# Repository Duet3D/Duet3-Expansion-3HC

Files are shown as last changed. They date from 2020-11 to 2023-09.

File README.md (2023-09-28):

# Duet3-Expansion-3HC
The Duet 3 Expansion 3HC board connects to the Duet 3 CAN-FD bus and provides 3 high current stepper driver channels, along with heaters, fans and GPIO. Multiple expansion boards can be daisy chained on the CAN-FD bus.



Product page is here: https://www.duet3d.com/Duet3Expansion3HC

Documentation is here: https://docs.duet3d.com/Duet3D_hardware/Duet_3_family/Duet_3_Mainboard_3HC_Hardware_Overview

As always please discuss this on the Duet3d forum: https://forum.duet3d.com/

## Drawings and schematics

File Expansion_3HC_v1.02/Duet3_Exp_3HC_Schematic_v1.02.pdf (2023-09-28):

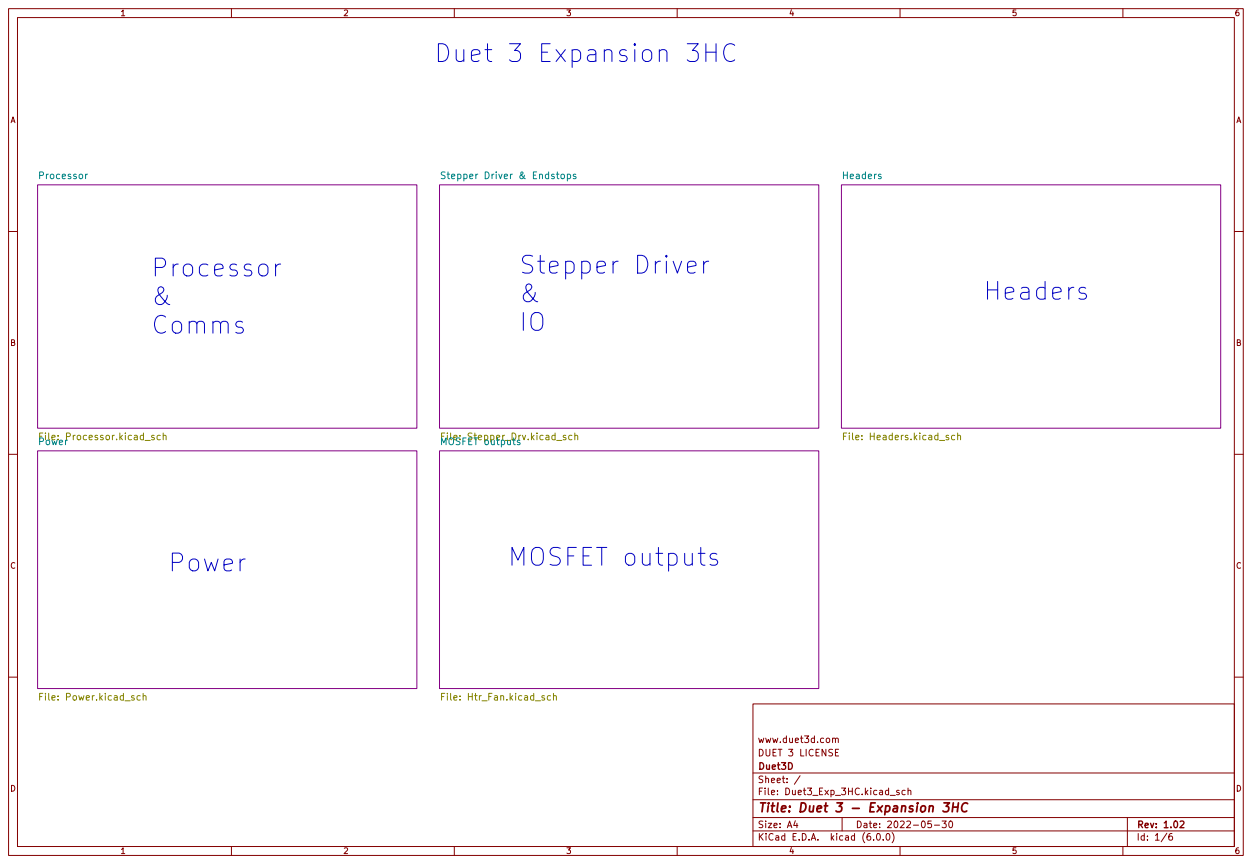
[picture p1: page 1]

Processor File: Processor.kicad_sch Power File: Power.kicad_sch

DUET 3 LICENSE www.duet3d.com

Id: 1/6 Title: Duet 3 - Expansion 3HC

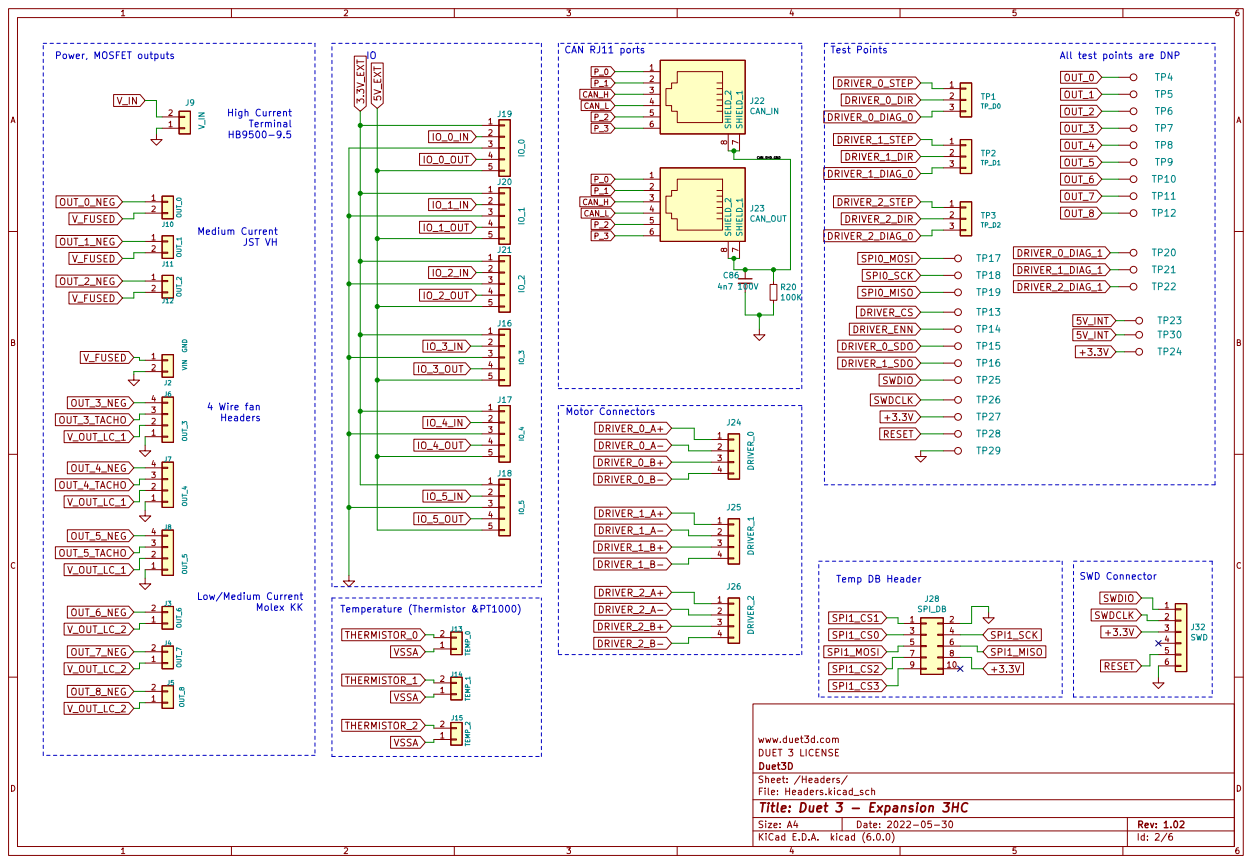
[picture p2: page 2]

Low/Medium Current Molex KK

DUET 3 LICENSE www.duet3d.com

File: Headers.kicad_sch Sheet: /Headers/ Duet3D

Id: 2/6 Title: Duet 3 - Expansion 3HC

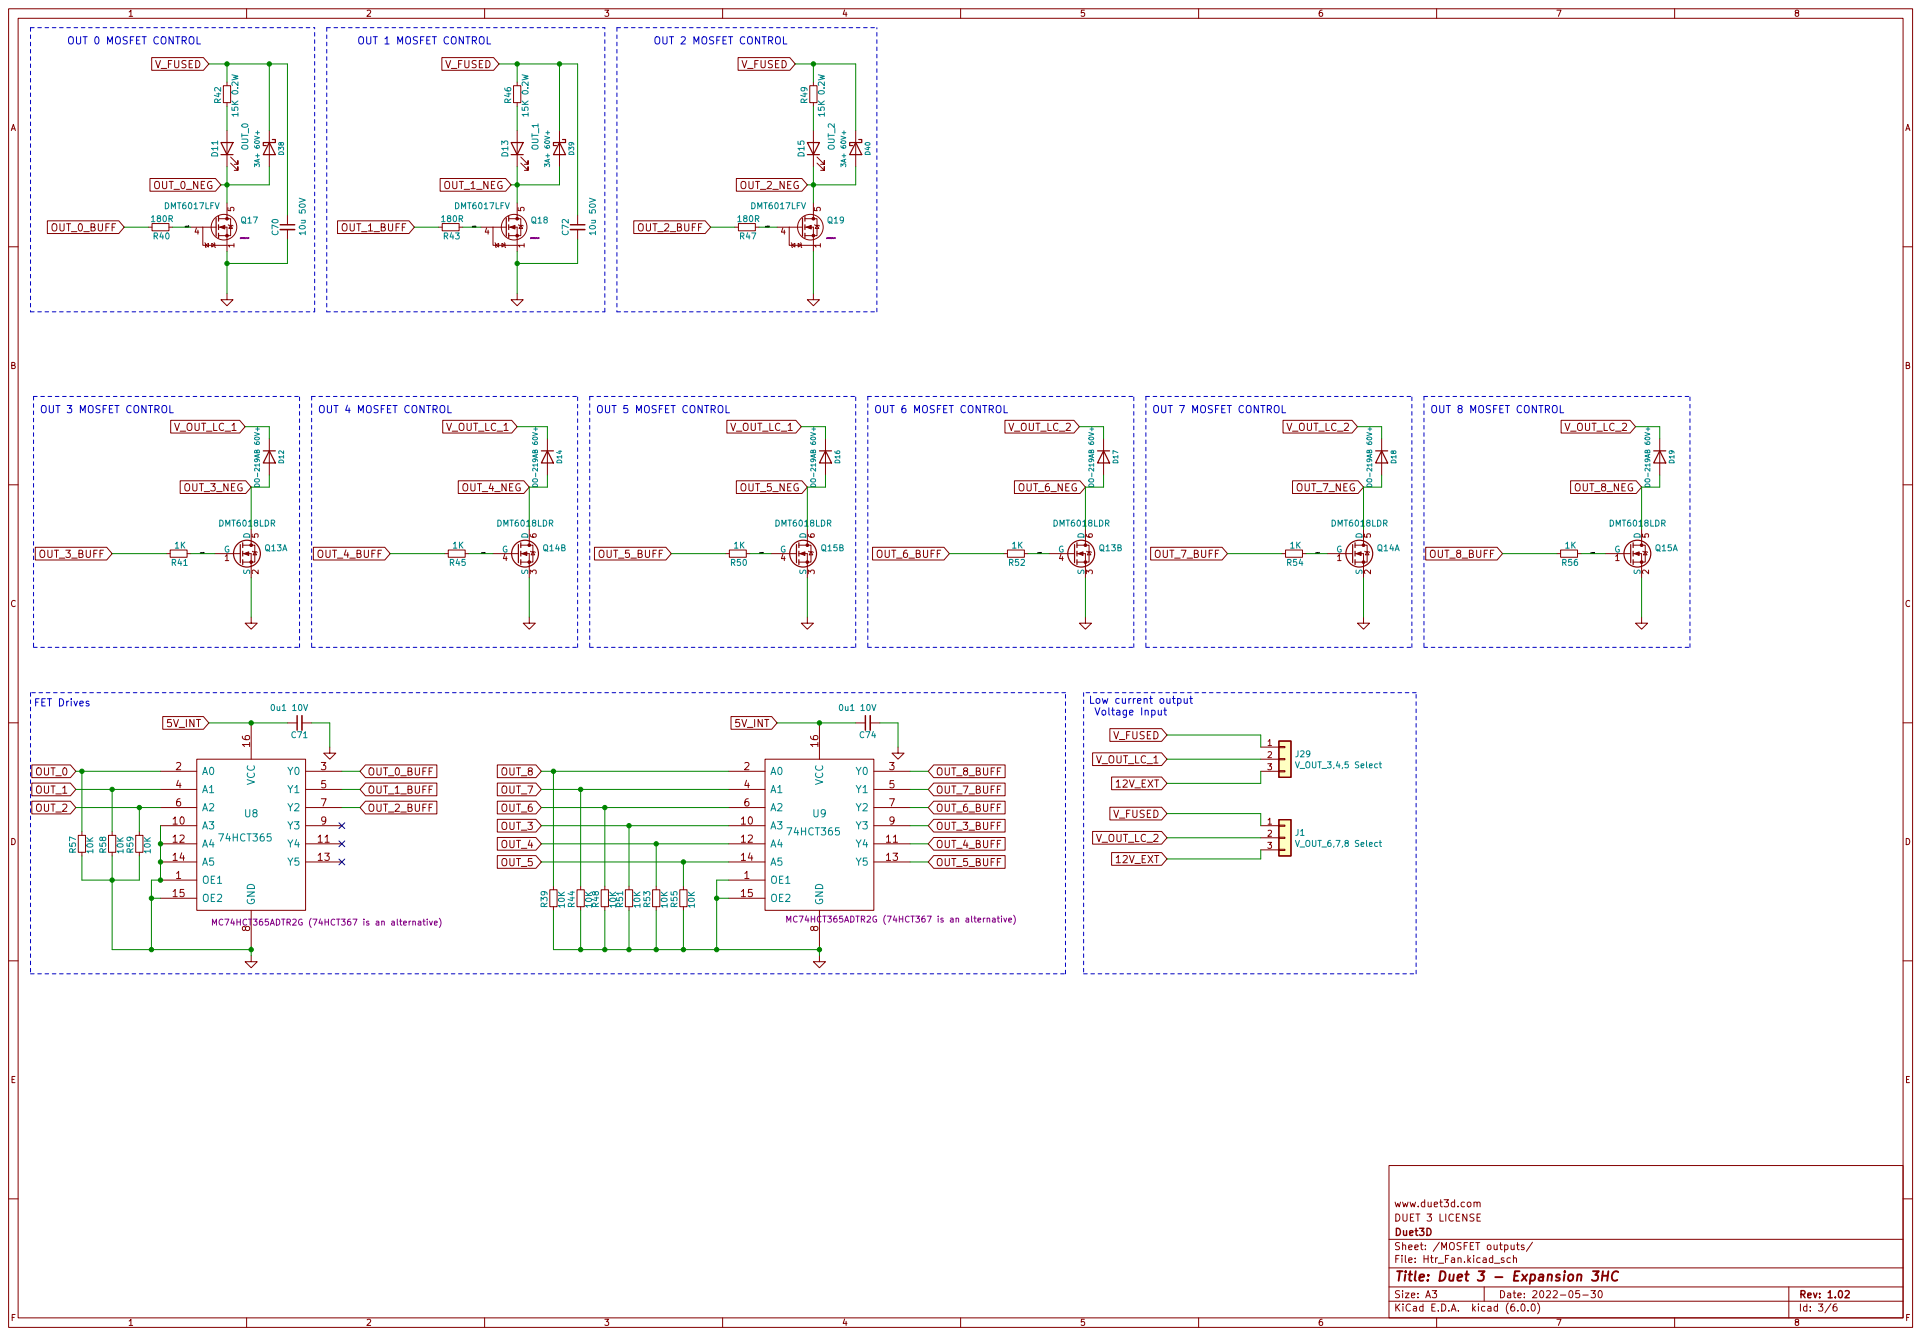
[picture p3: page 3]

DUET 3 LICENSE www.duet3d.com

File: Htr_Fan.kicad_sch
Id: 3/6 Title: Duet 3 - Expansion 3HC

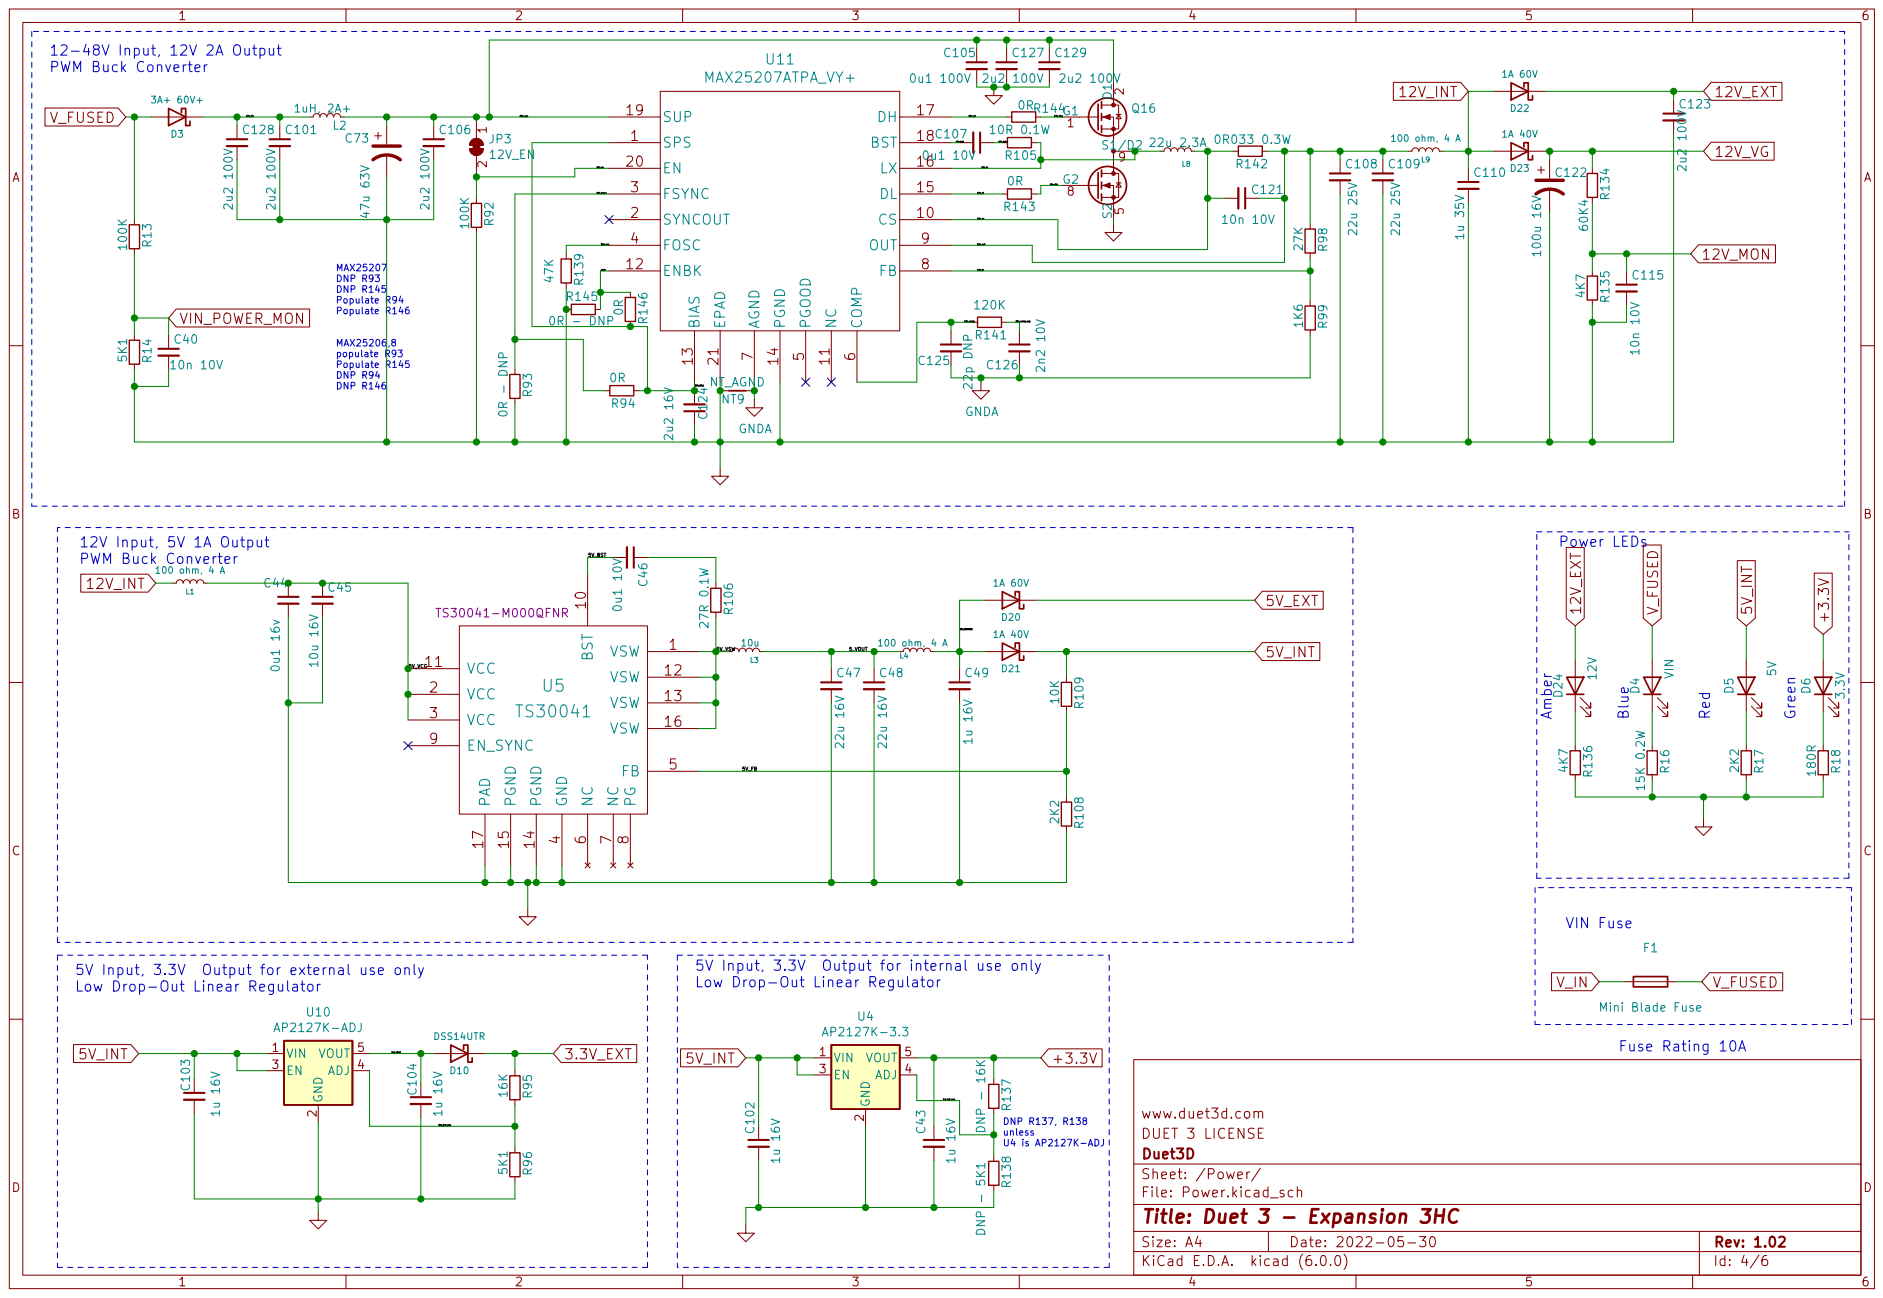
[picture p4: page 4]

MAX25207 DNP R93 DNP R145 Populate R94 Populate R146 MAX25206,8

5V_BST 5V Input, 3.3V Output for external use only
12V_INT

5V Input, 3.3V Output for internal use only
Low Drop-Out Linear Regulator

2 EN 3 ADJ 4 VOUT 5 U10 AP2127K-ADJ

DUET 3 LICENSE www.duet3d.com

File: Power.kicad_sch Sheet: /Power/ Duet3D

Id: 4/6 Title: Duet 3 - Expansion 3HC

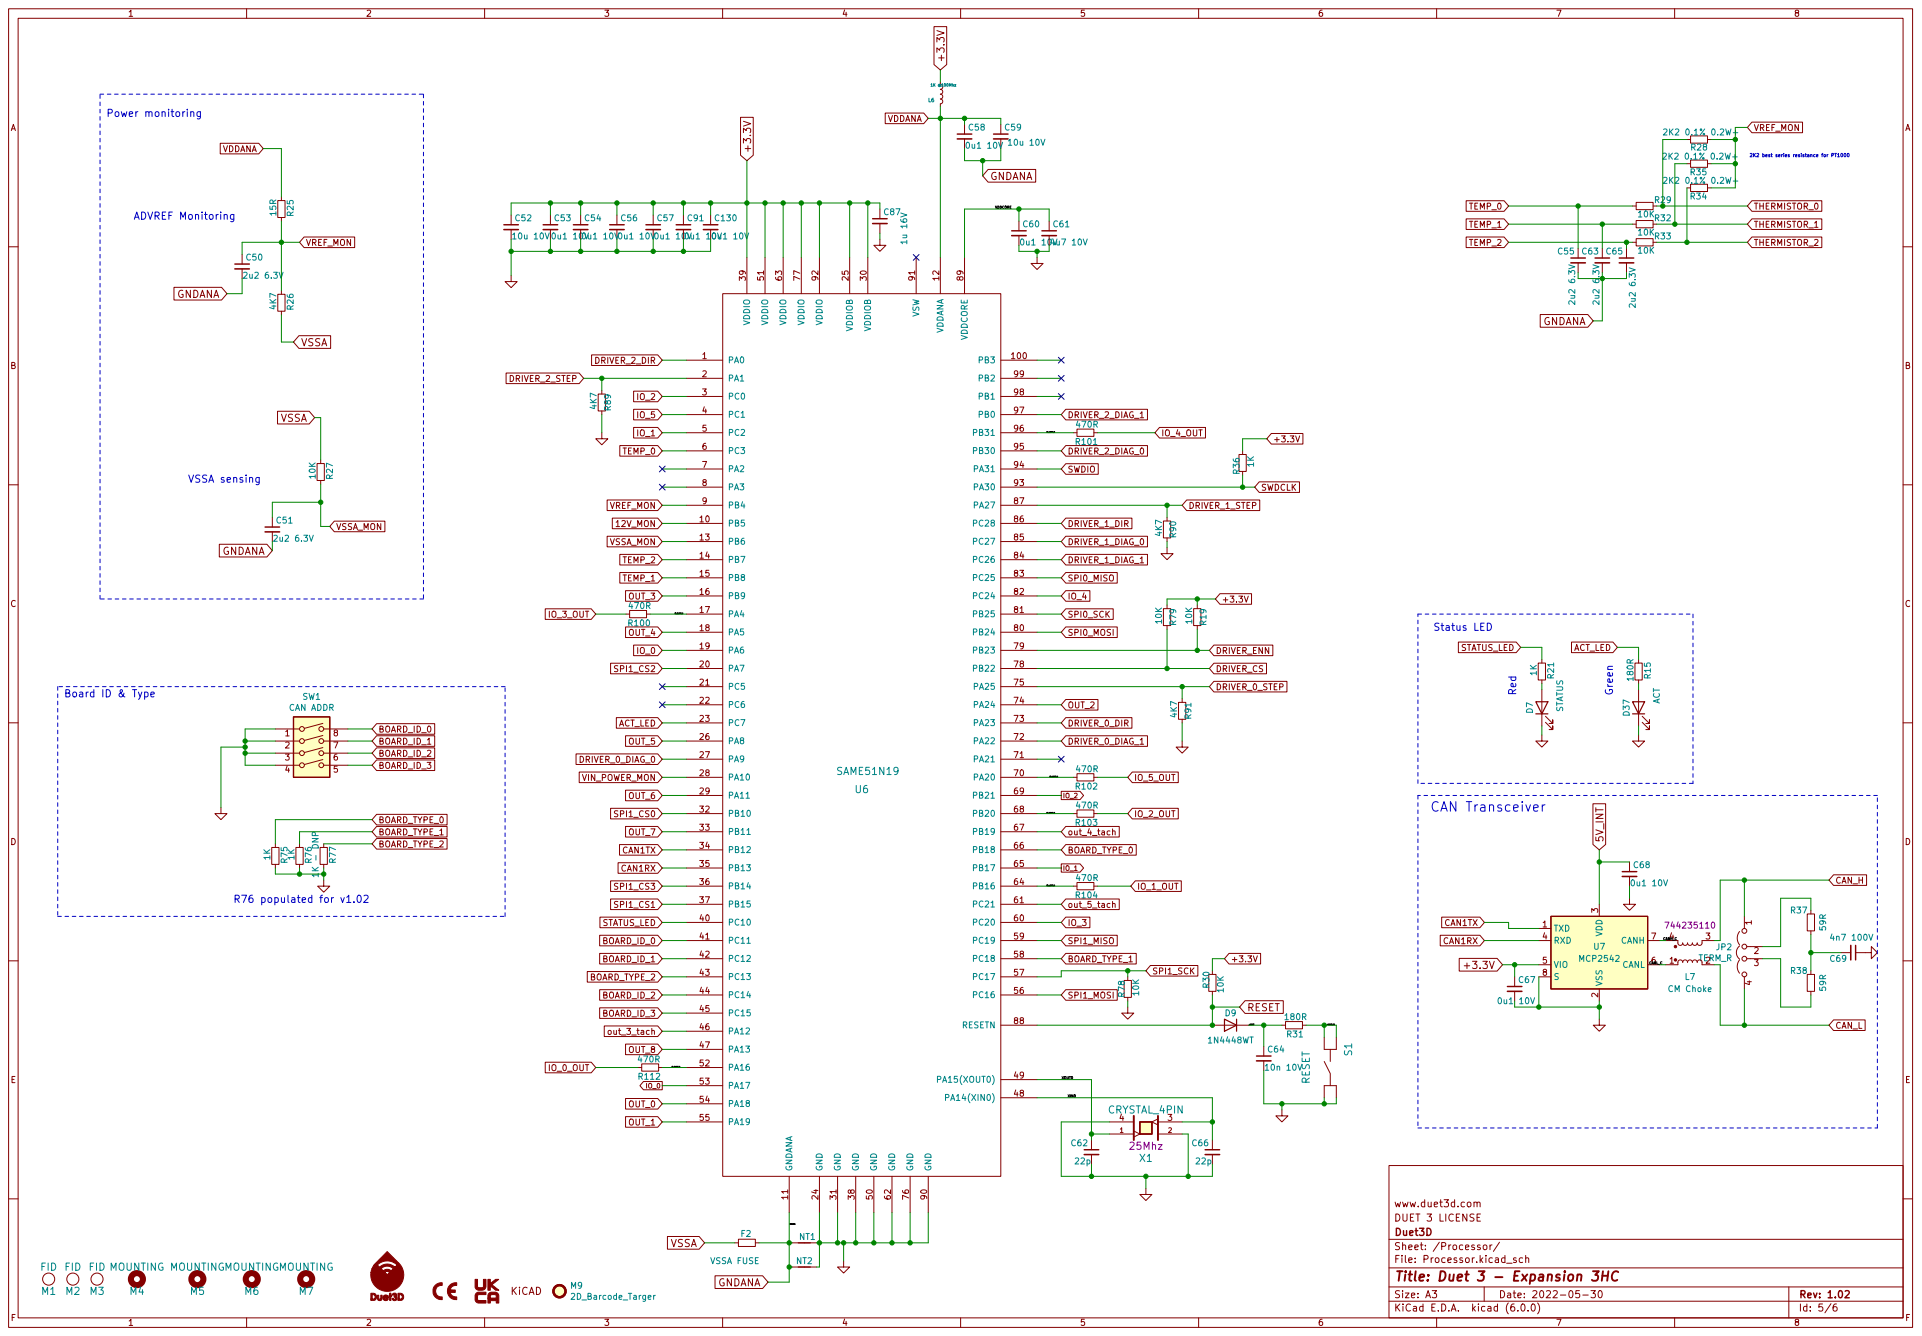
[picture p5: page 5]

2K2 best series resistance for PT1000 Power monitoring
VREF_MON VSSA

DUET 3 LICENSE www.duet3d.com

GNDANA

File: Processor.kicad_sch Sheet: /Processor/ Duet3D

Id: 5/6 Title: Duet 3 - Expansion 3HC

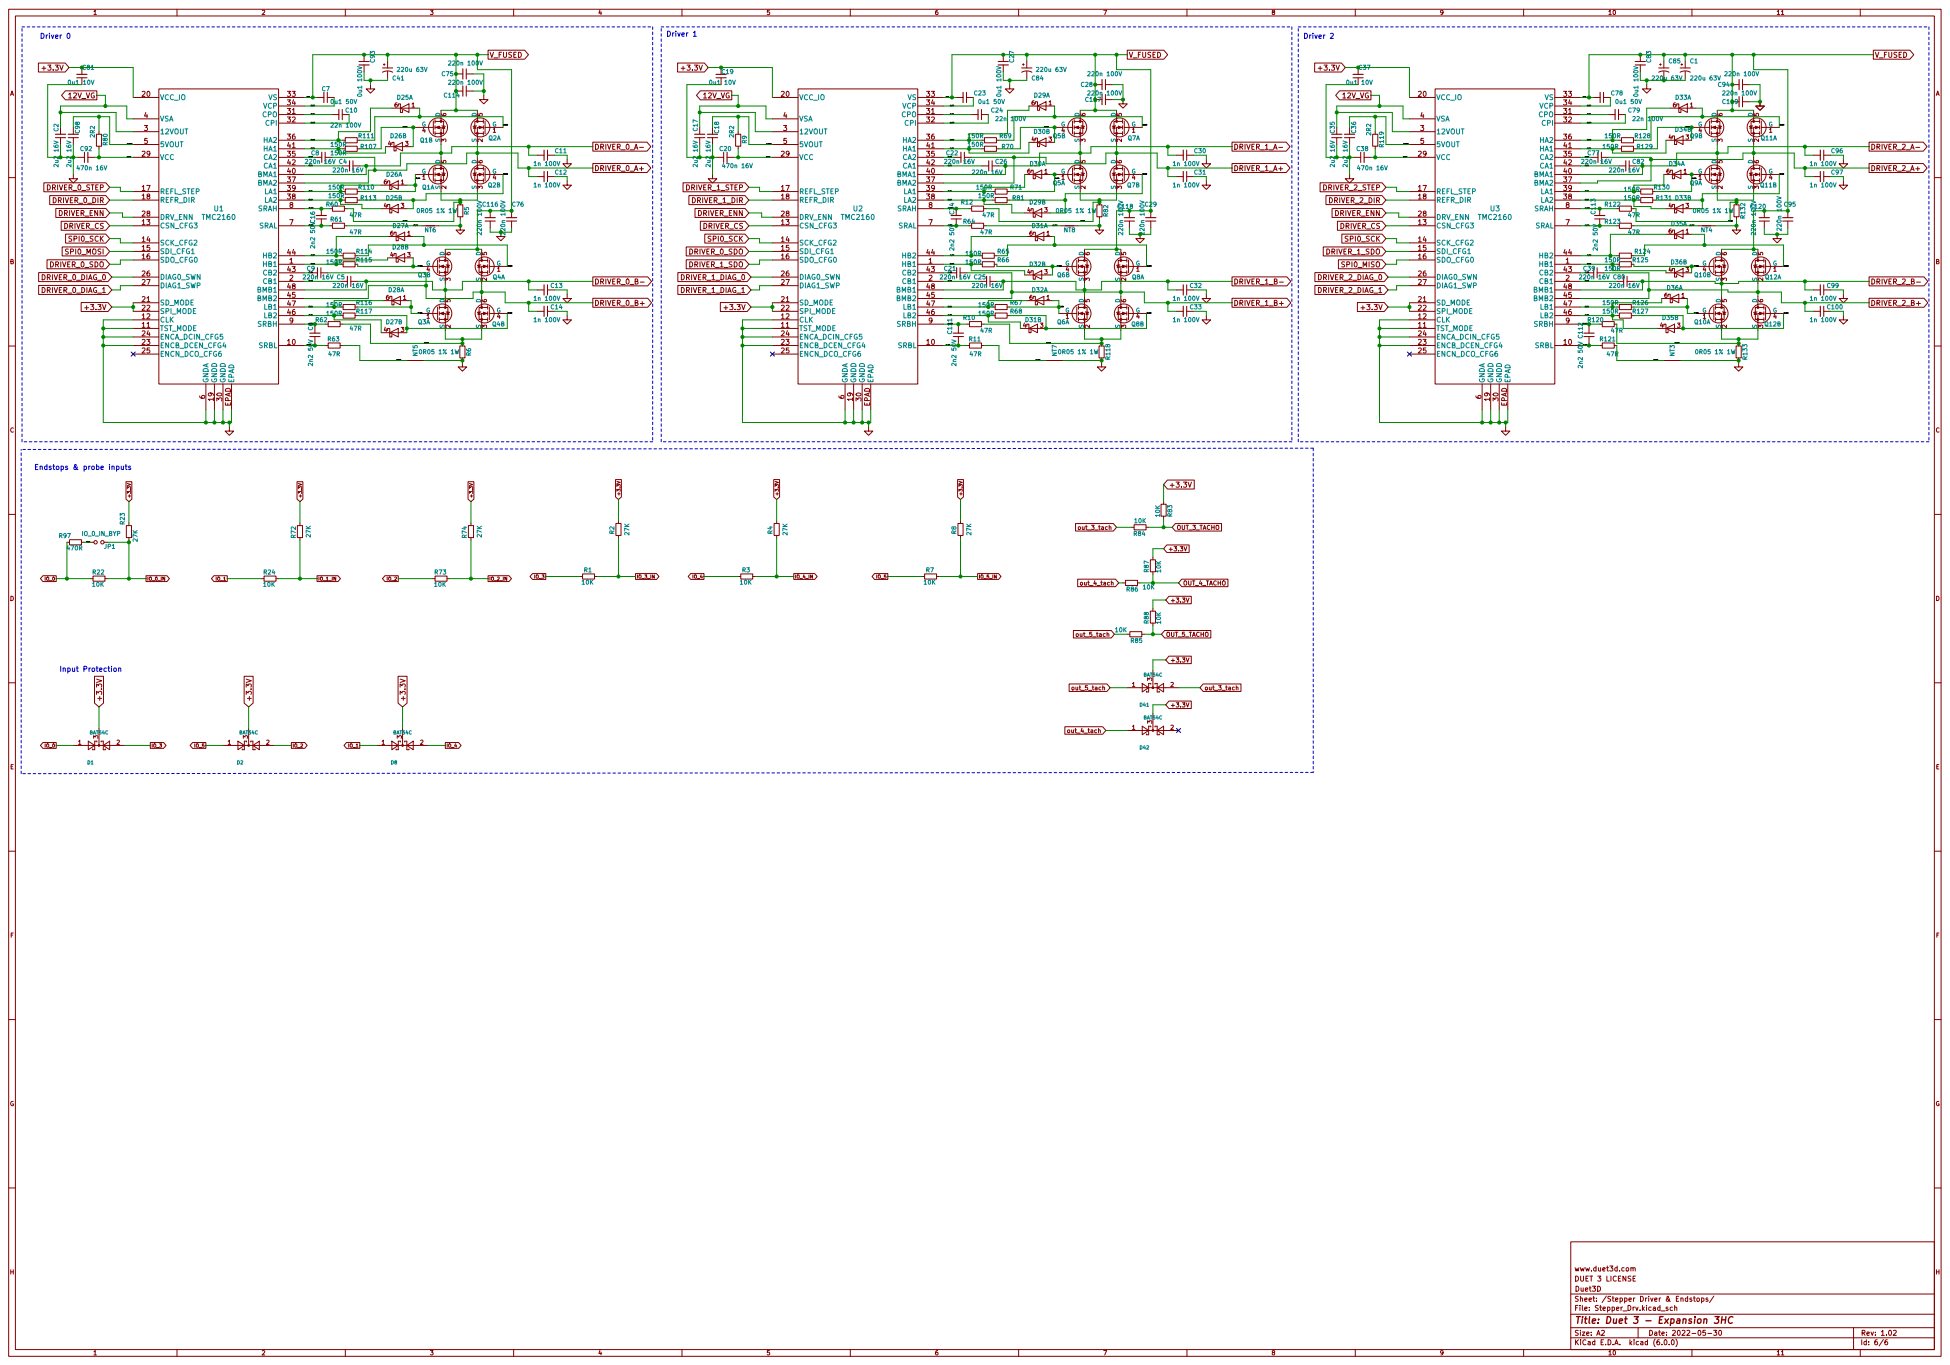
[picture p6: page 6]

6 SRAL 7 SRAH 8 SRBH 9 EPAD EPAD U1 TMC2160 R62

6 SRAL 7 SRAH 8 SRBH 9 EPAD EPAD U2 TMC2160

DUET 3 LICENSE www.duet3d.com

Sheet: /Stepper Driver & Endstops/ Duet3D

File: Stepper_Drv.kicad_sch
Id: 6/6 Title: Duet 3 - Expansion 3HC

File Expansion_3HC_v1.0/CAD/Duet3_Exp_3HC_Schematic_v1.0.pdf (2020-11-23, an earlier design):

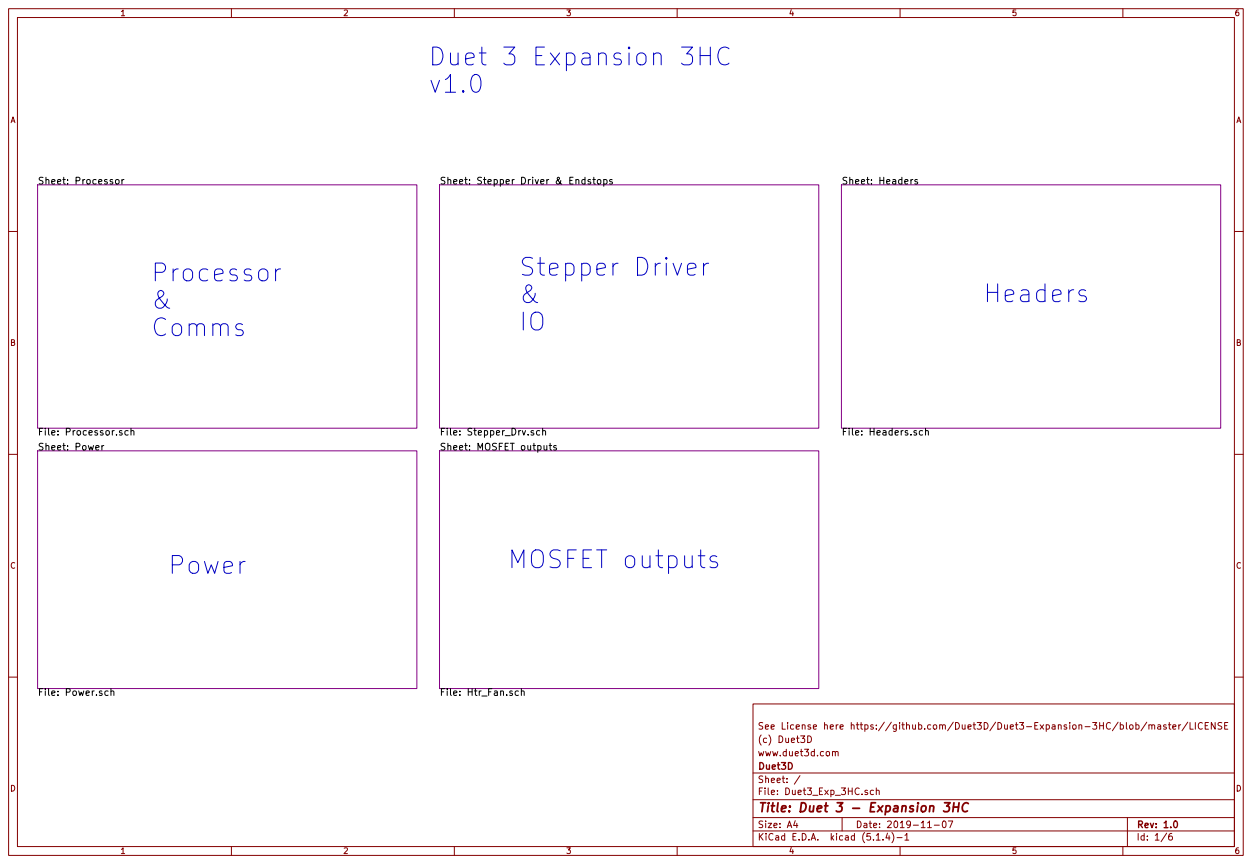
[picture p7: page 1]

Sheet: Headers File: Headers.sch Sheet: Power File: Power.sch

Sheet: Stepper Driver & Endstops

See License here https://github.com/Duet3D/Duet3-Expansion-3HC/blob/master/LICENSE
(c) Duet3D
www.duet3d.com
File: Duet3_Exp_3HC.sch Sheet: / Duet3D

Id: 1/6 Title: Duet 3 - Expansion 3HC

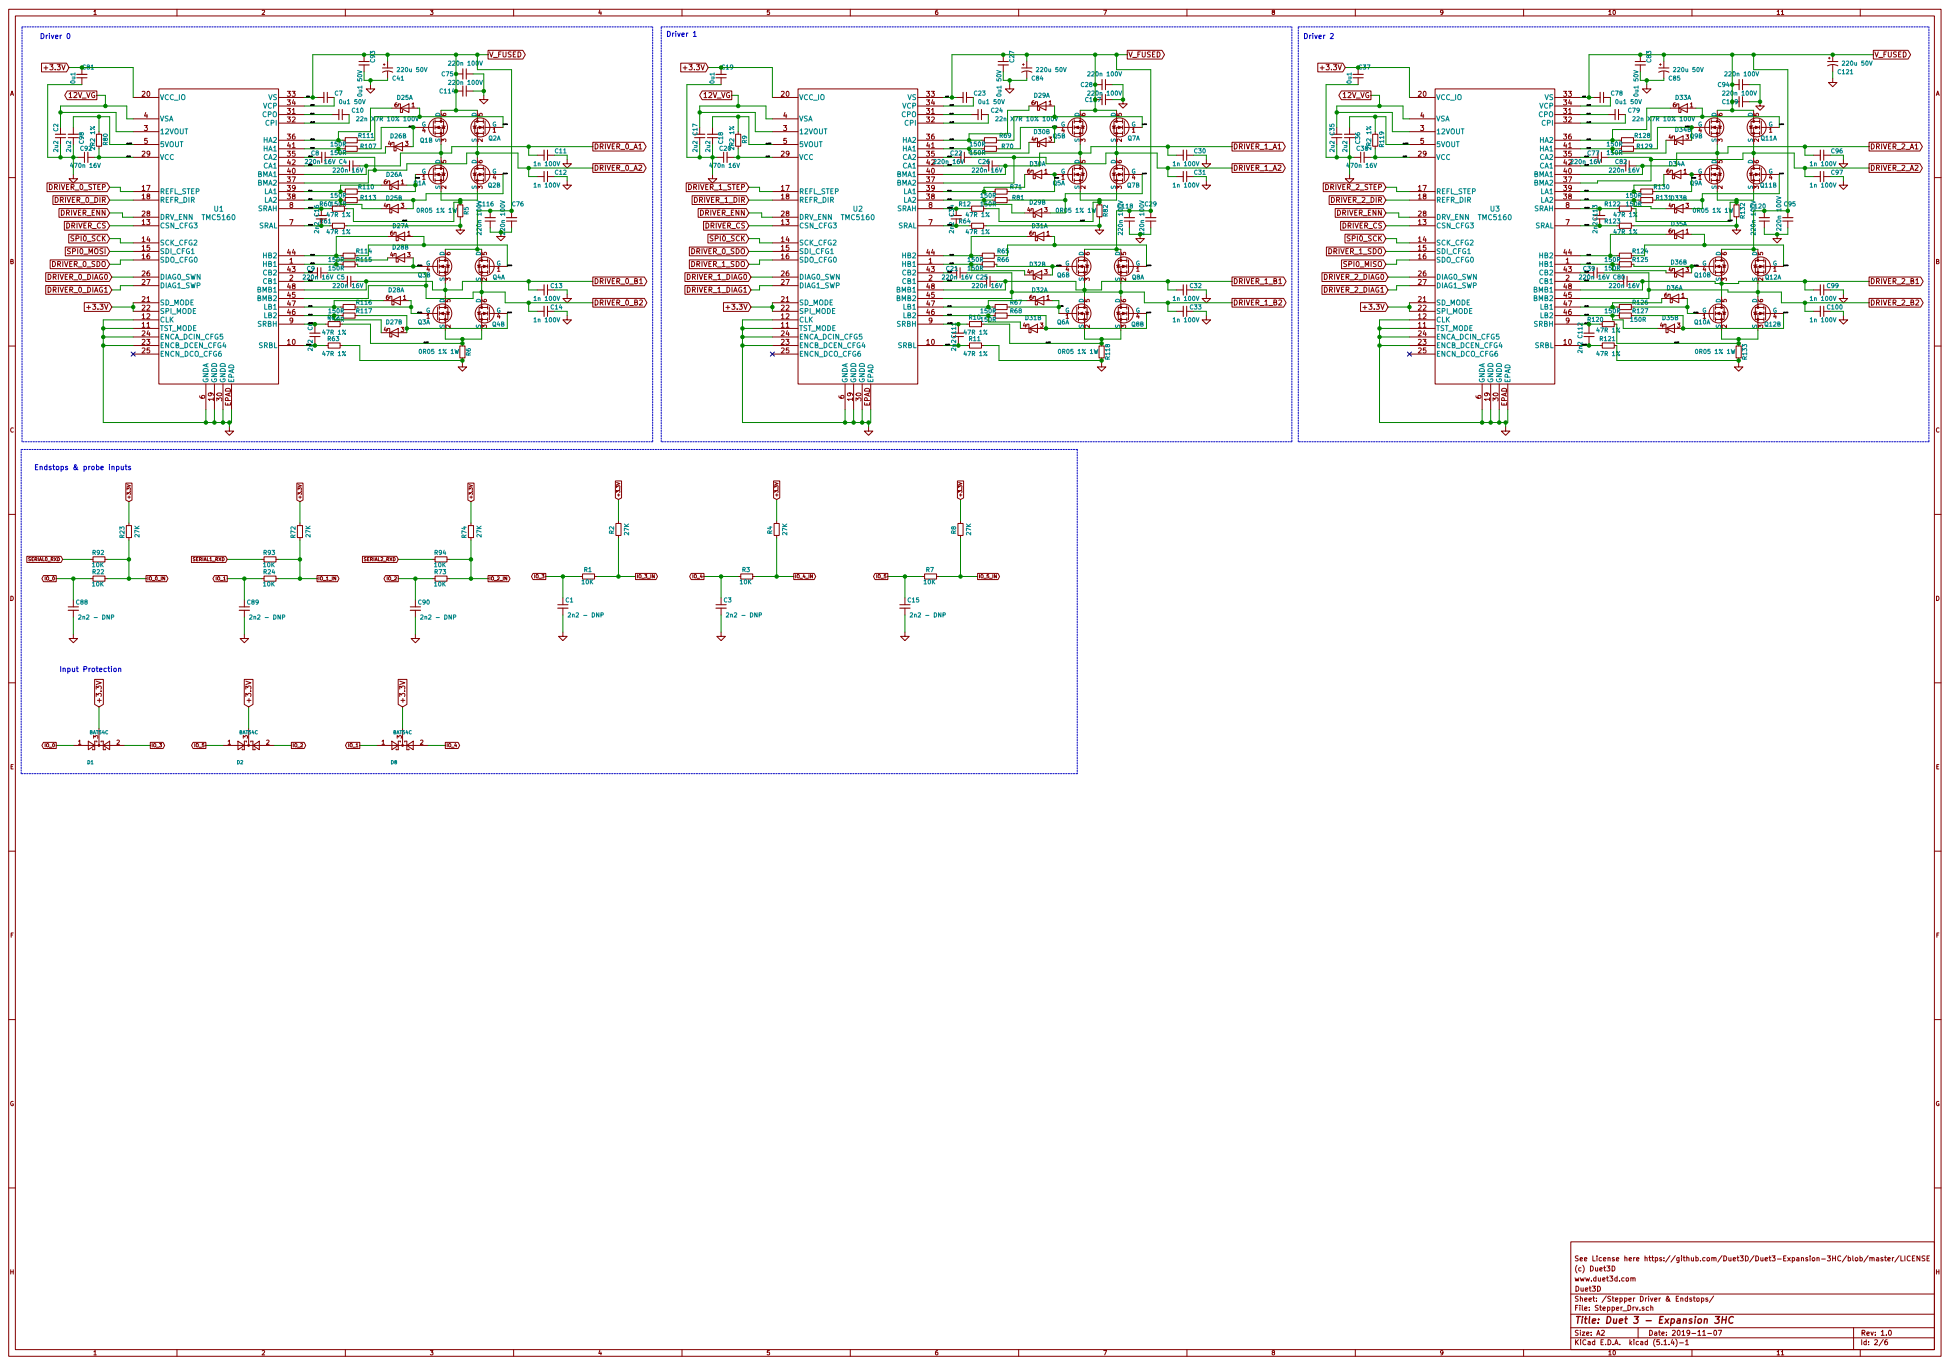
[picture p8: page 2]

6 SRAL 7 SRAH 8 SRBH 9 EPAD EPAD U2 TMC5160 C18 2u2 C20

6 SRAL 7 SRAH 8 SRBH 9 EPAD EPAD U1 TMC5160 C29 220n 100V R67

See License here https://github.com/Duet3D/Duet3-Expansion-3HC/blob/master/LICENSE
(c) Duet3D
www.duet3d.com
Sheet: /Stepper Driver & Endstops/ Duet3D

File: Stepper_Drv.sch
Id: 2/6 Title: Duet 3 - Expansion 3HC

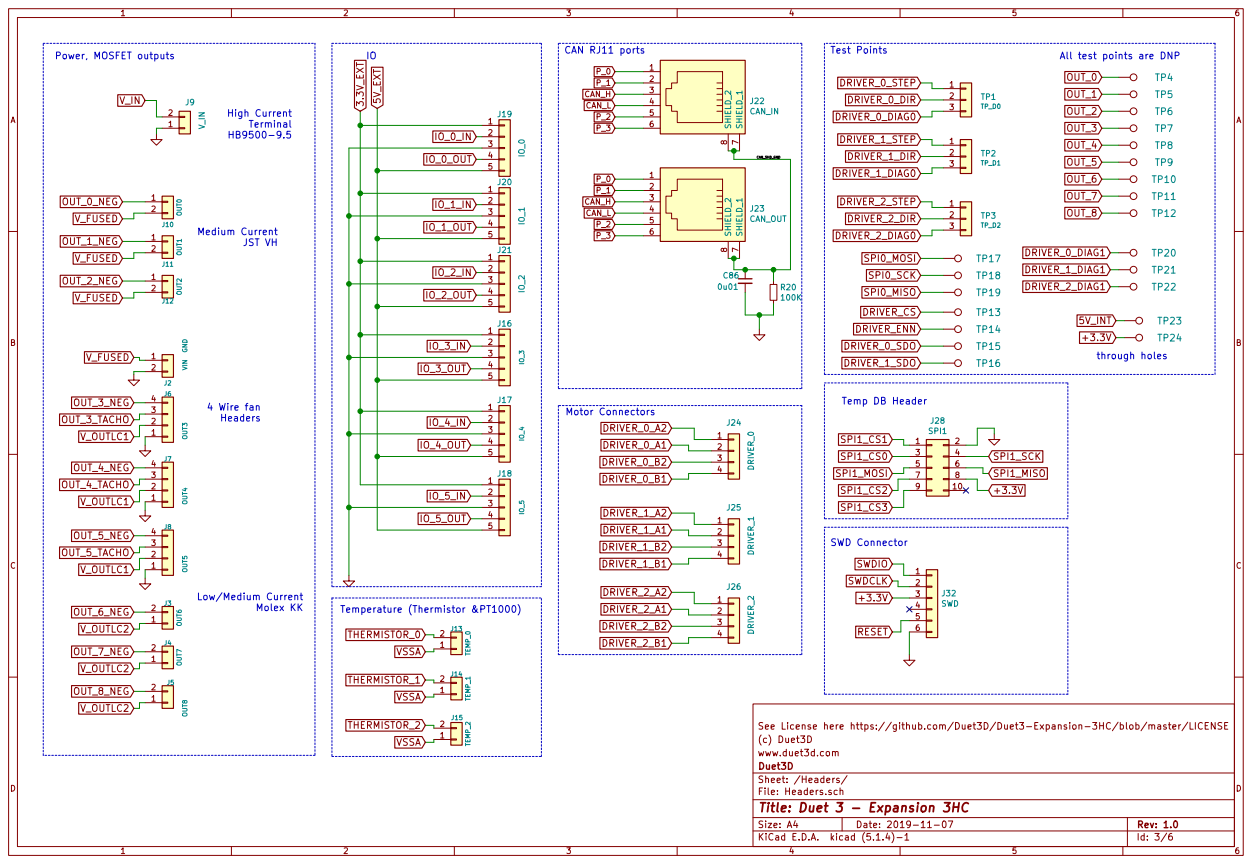
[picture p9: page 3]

Low/Medium Current Molex KK

See License here https://github.com/Duet3D/Duet3-Expansion-3HC/blob/master/LICENSE
(c) Duet3D
www.duet3d.com
File: Headers.sch Sheet: /Headers/ Duet3D

Id: 3/6 Title: Duet 3 - Expansion 3HC

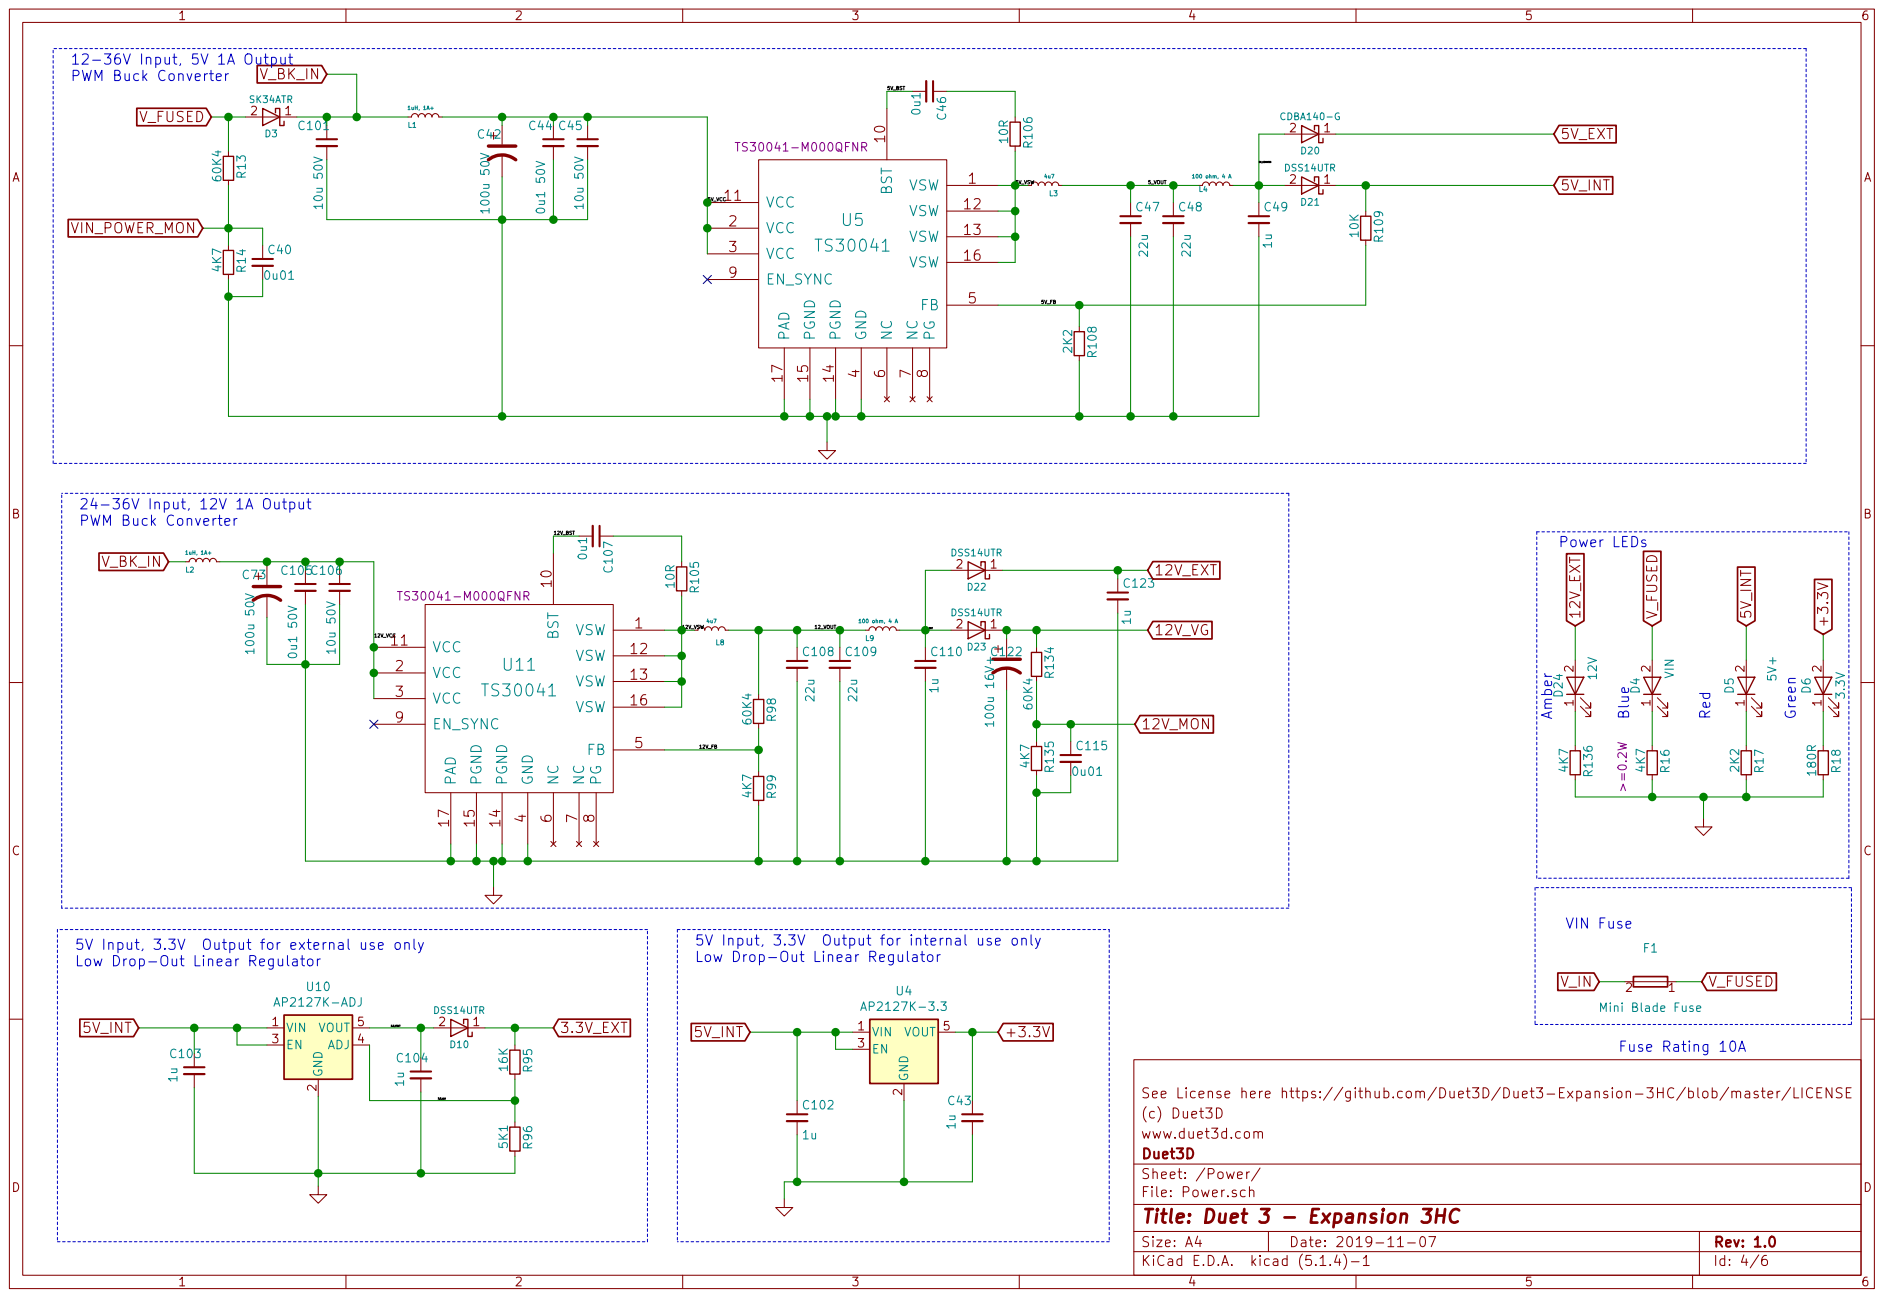
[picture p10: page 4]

2 EN 3 ADJ 4 VOUT 5 U10 AP2127K-ADJ C103 1u R105 10R R106 10R 60K4 R98 4K7 R99 C104 1u R109 10K

5V Input, 3.3V Output for external use only

5V Input, 3.3V Output for internal use only
Low Drop-Out Linear Regulator

See License here https://github.com/Duet3D/Duet3-Expansion-3HC/blob/master/LICENSE
(c) Duet3D
www.duet3d.com
File: Power.sch Sheet: /Power/ Duet3D

Id: 4/6 Title: Duet 3 - Expansion 3HC

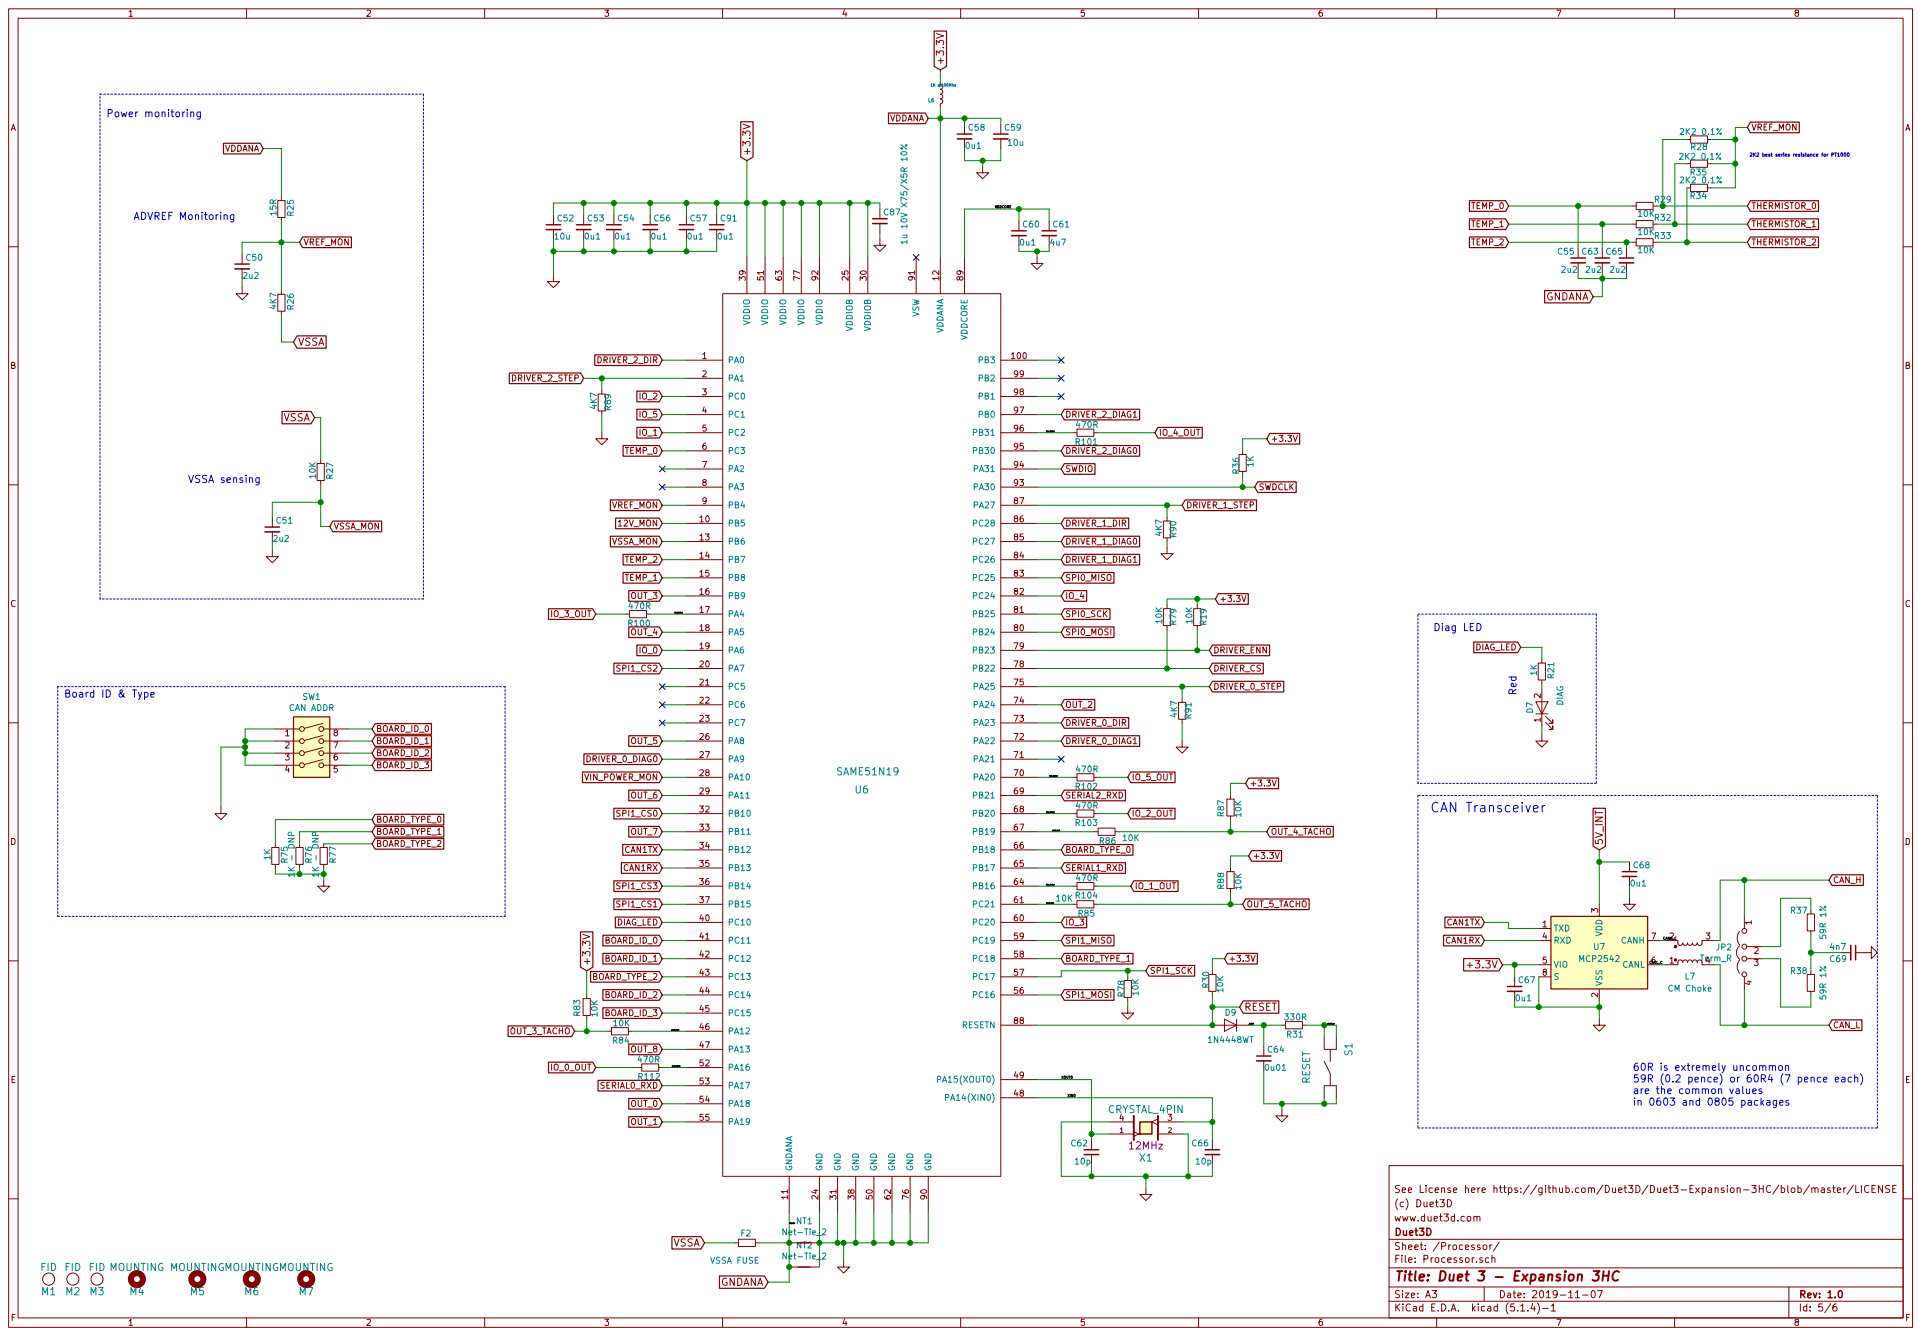
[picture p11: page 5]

2K2 best series resistance for PT1000 Red

60R is extremely uncommon
59R (0.2 pence) or 60R4 (7 pence each) are the common values

(c) Duet3D
www.duet3d.com
File: Processor.sch Sheet: /Processor/ Duet3D

Id: 5/6 Title: Duet 3 - Expansion 3HC

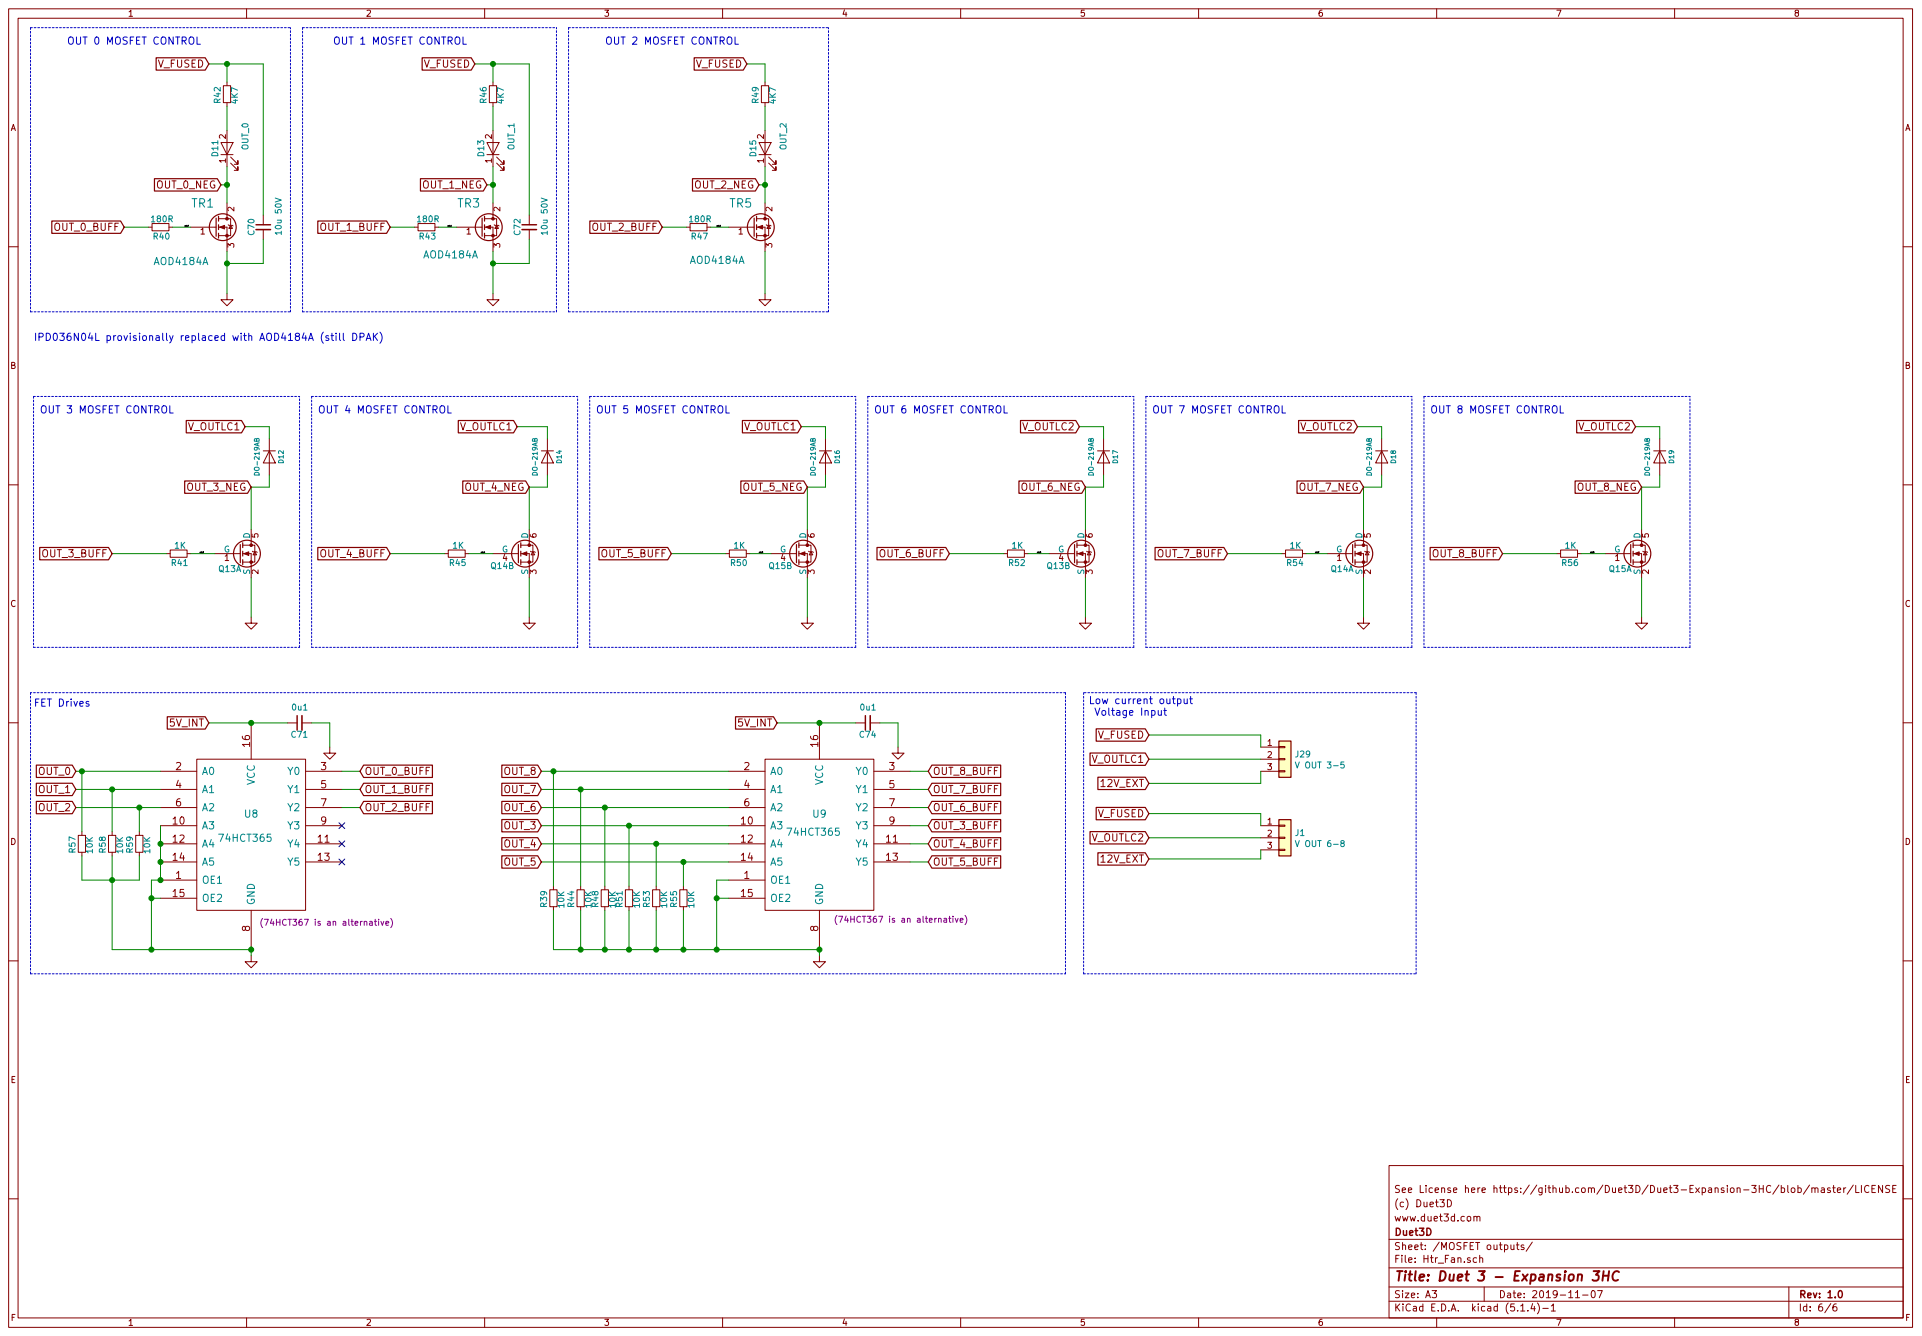
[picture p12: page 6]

IPD036N04L provisionally replaced with AOD4184A (still DPAK)

(74HCT367 is an alternative) D14 DO-219AB C71

See License here https://github.com/Duet3D/Duet3-Expansion-3HC/blob/master/LICENSE
(c) Duet3D
www.duet3d.com
Sheet: /MOSFET outputs/ Duet3D

File: Htr_Fan.sch
Id: 6/6 Title: Duet 3 - Expansion 3HC

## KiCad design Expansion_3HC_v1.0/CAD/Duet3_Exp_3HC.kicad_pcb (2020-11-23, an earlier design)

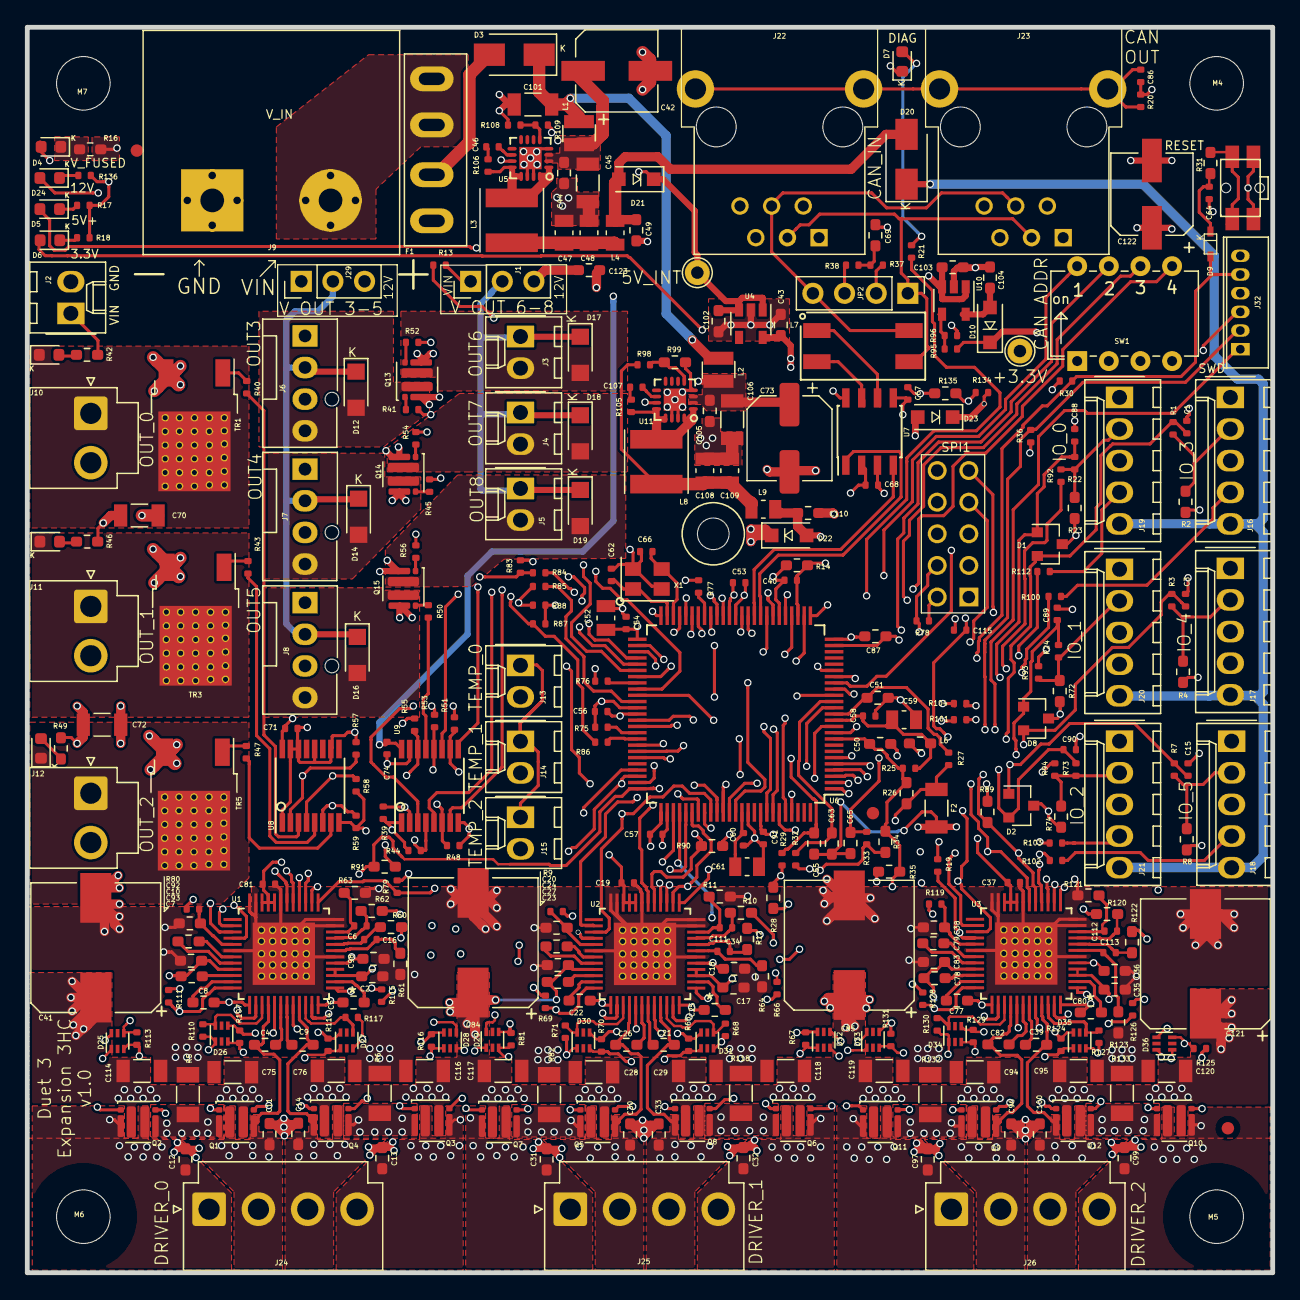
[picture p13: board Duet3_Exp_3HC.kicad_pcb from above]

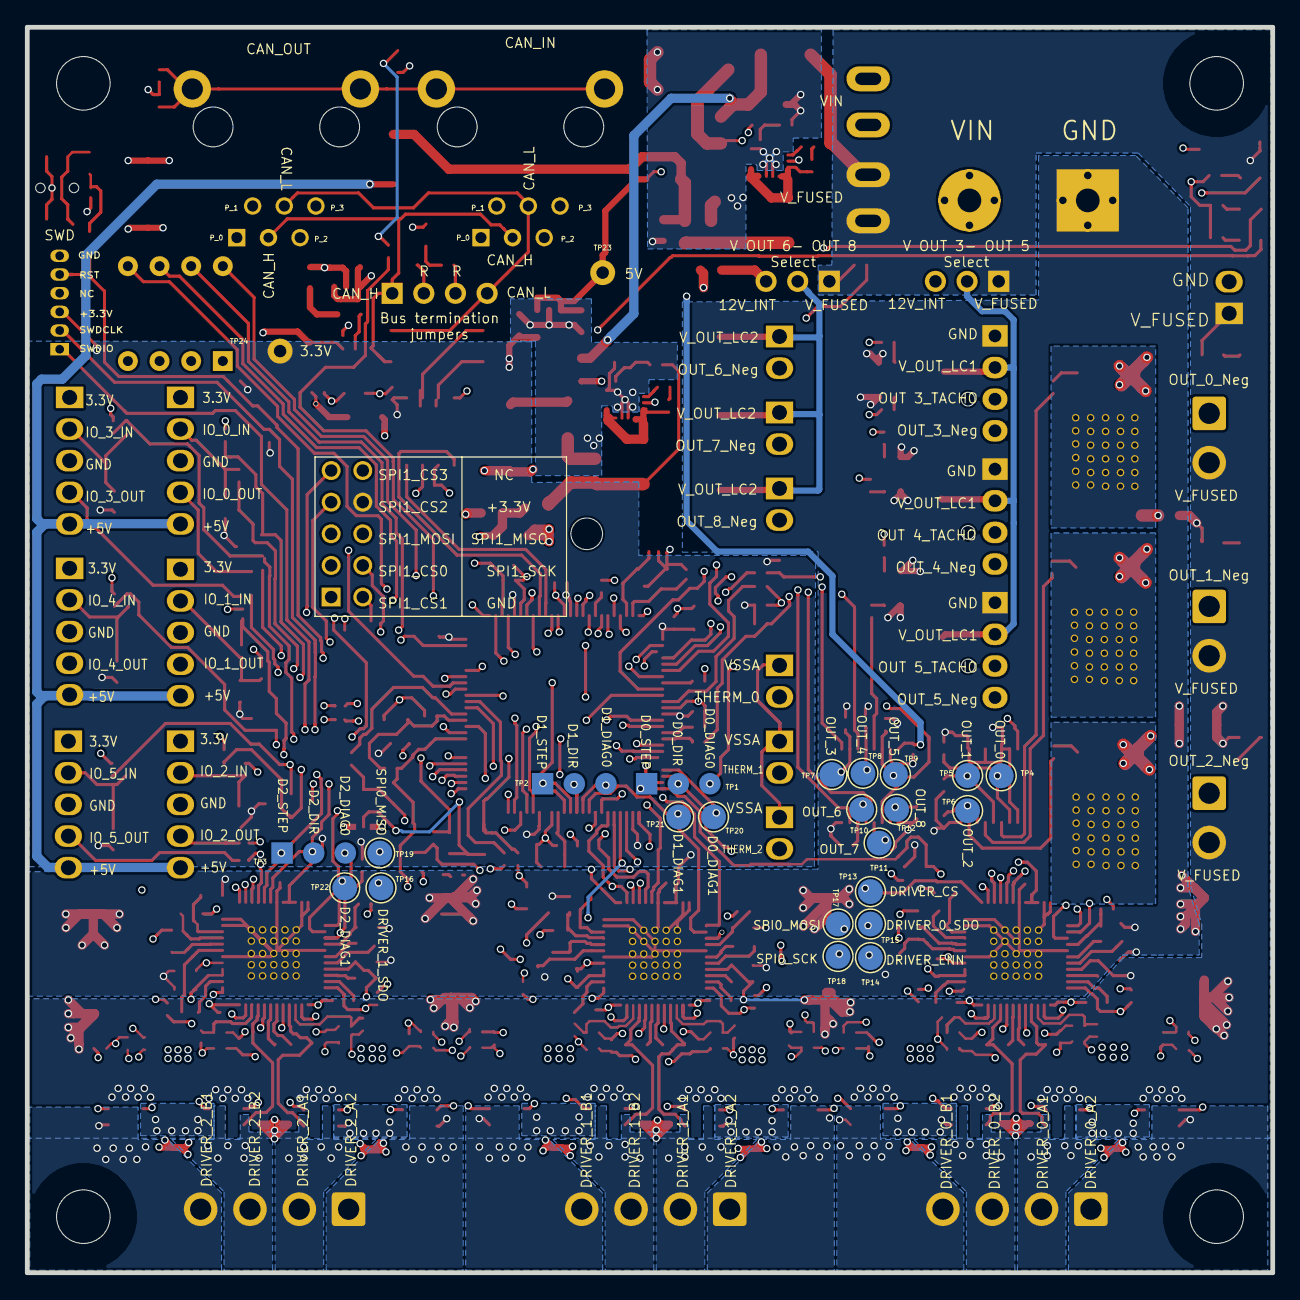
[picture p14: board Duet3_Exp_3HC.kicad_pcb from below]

Board: 4 copper layers, 100.0 x 100.0 mm, 398 parts (19 on the bottom side), 279 nets.

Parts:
C1, C3, C15, C88, C89, C90: 2n2 - DNP; C_0402_1005Metric_Wbry
C2, C17, C18, C35, C36, C50, C51, C55, C63, C65, C98: 2u2; C_0603_1608Metric_Wbry
C4, C5, C8, C9, C21, C22, C25, C26, C39, C77, C80, C82: 220n 16V; C_0603_1608Metric_Wbry
C6, C16, C34, C111, C112, C113: 2n2; C_0402_1005Metric_Wbry
C7, C23, C27, C44, C78, C83, C93, C105: 0u1 50V; C_0603_1608Metric_Wbry
C10, C24, C79: 22n X7R 10% 100V; C_0603_1608Metric_Wbry
C11, C12, C13, C14, C30, C31, C32, C33, C96, C97, C99, C100: 1n 100V; C_0603_1608Metric_Wbry
C19, C37, C46, C53, C54, C56, C57, C58, C60, C67, C68, C71, C74, C81, C91, C107: 0u1; C_0402_1005Metric_Wbry
C20, C38, C92: 470n 16V; C_0603_1608Metric_Wbry
C28, C29, C75, C76, C94, C95, C114, C116, C117, C118, C119, C120: 220n 100V; C_1206_3216Metric
C40, C64, C86, C115: 0u01; C_0402_1005Metric_Wbry
C41, C84, C85, C121: 220u 50V; CP_Elec_10x10
C42, C73: 100u 50V; CP_Elec_6.3x7.7
C43, C49, C102, C103, C104, C110, C123: 1u; C_0603_1608Metric_Wbry
C45, C70, C72, C101, C106: 10u 50V; C_1206_3216Metric
C47, C48, C108, C109: 22u; C_0805_2012Metric
C52, C59: 10u; C_0805_2012Metric
C61: 4u7; C_0805_2012Metric
C62, C66: 10p; C_0402_1005Metric_Wbry
C69: 4n7; C_0603_1608Metric_Wbry
C87: 1u 10V X75/X5R 10%; C_0603_1608Metric_Wbry
C122: 100u 16V+; CP_Elec_6.3x7.7
D1, D2, D8: BAT54C; SOT-23
D3: SK34ATR; D_SMA
D4: V_FUSED; LED_0603_1608Metric
D5: 5V+; LED_0603_1608Metric
D6: 3.3V; LED_0603_1608Metric
D7: DIAG; LED_0603_1608Metric
D9: 1N4448WT; SOD-523F
D10, D21, D22, D23: DSS14UTR; D_SOD-123F
D11: OUT_0; LED_0603_1608Metric
D12, D14, D16, D17, D18, D19: DO-219AB
D13: OUT_1; LED_0603_1608Metric
D15: OUT_2; LED_0603_1608Metric
D20: CDBA140-G; D_SMA
D24: 12V; LED_0603_1608Metric
D25, D26, D27, D28, D29, D30, D31, D32, D33, D34, D35, D36: BAT40V; SOT-563
F1: Mini Blade Fuse; MCCQ-122-minibladefuseholder
F2: VSSA FUSE; Fuse_1206_3216Metric
J1: V OUT 6-8; PinHeader_1x03_P2.54mm_Vertical
J2: VIN GND; Wurth_61900211121-1x02_P2.54mm_Vertical-(Molex_KK-254_AE-64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
J3: OUT6; Wurth_61900211121-1x02_P2.54mm_Vertical-(Molex_KK-254_AE-64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
J4: OUT7; Wurth_61900211121-1x02_P2.54mm_Vertical-(Molex_KK-254_AE-64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
J5: OUT8; Wurth_61900211121-1x02_P2.54mm_Vertical-(Molex_KK-254_AE-64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
J6: OUT3; FanPinHeader_1x04_P2.54mm_Vertical
J7: OUT4; FanPinHeader_1x04_P2.54mm_Vertical
J8: OUT5; FanPinHeader_1x04_P2.54mm_Vertical
J9: V_IN; screwt-barrier-9.5mm-1x2
J10: OUT0; JST_VH_B2P-VH-B_1x02_P3.96mm_Vertical
J11: OUT1; JST_VH_B2P-VH-B_1x02_P3.96mm_Vertical
J12: OUT2; JST_VH_B2P-VH-B_1x02_P3.96mm_Vertical
J13: TEMP_0; Wurth_61900211121-1x02_P2.54mm_Vertical-(Molex_KK-254_AE-64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
J14: TEMP_1; Wurth_61900211121-1x02_P2.54mm_Vertical-(Molex_KK-254_AE-64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
J15: TEMP_2; Wurth_61900211121-1x02_P2.54mm_Vertical-(Molex_KK-254_AE-64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
J16: IO_3; Wurth_61900511121-1x05_P2.54mm_Vertical(Molex_KK-254_AE-641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
J17: IO_4; Wurth_61900511121-1x05_P2.54mm_Vertical(Molex_KK-254_AE-641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
J18: IO_5; Wurth_61900511121-1x05_P2.54mm_Vertical(Molex_KK-254_AE-641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
J19: IO_0; Wurth_61900511121-1x05_P2.54mm_Vertical(Molex_KK-254_AE-641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
J20: IO_1; Wurth_61900511121-1x05_P2.54mm_Vertical(Molex_KK-254_AE-641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
J21: IO_2; Wurth_61900511121-1x05_P2.54mm_Vertical(Molex_KK-254_AE-641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
J22: CAN_IN; RJ11_6P6C_half_shield
J23: CAN_OUT; RJ11_6P6C_half_shield
J24: DRIVER_0; JST_VH_B4P-VH_1x04_P3.96mm_Vertical
J25: DRIVER_1; JST_VH_B4P-VH_1x04_P3.96mm_Vertical
J26: DRIVER_2; JST_VH_B4P-VH_1x04_P3.96mm_Vertical
J28: SPI1; MAX_TEMP_DB
J29: V OUT 3-5; PinHeader_1x03_P2.54mm_Vertical
J32: SWD; JST_ZH_1x06_P1.5_B6B-ZR-SM4-TF
JP2: Term_R; PinHeader_1x04_P2.54mm_Vertical
L1, L2: 1uH, 1A+; L_1008_2512Metric
L3, L8: 4u7; L_Taiyo-Yuden_NR-50xx
L4, L9: 100 ohm, 4 A; L_0805_2012Metric
L6: 1K @100Mhz; R_0603_1608Metric_Wbry
L7: CM Choke; DR331
M1, M2, M3: FID; Fiducial_1mm_Dia_2mm_Outer
M4, M5, M6, M7: MOUNTING; MountingHole_4.3mm_M4
NT1, NT2: Net-Tie_2; NetTie-2_SMD_Pad0.5mm
Q1, Q2, Q3, Q4, Q5, Q6, Q7, Q8, Q9, Q10, Q11, Q12, Q13, Q14, Q15: Q_DUAL_NMOS; Fairchild_DualPower33-6_3x3mm
R1, R3, R7, R19, R22, R24, R27, R29, R30, R32, R33, R39, R44, R48, R51, R53, R55, R57, R58, R59, R73, R78, R79, R83, R84, R85, R86, R87, R88, R92, R93, R94, R109: 10K; R_0402_1005Metric_Wbry
R2, R4, R8, R23, R72, R74: 27K; R_0603_1608Metric_Wbry
R5, R6, R82, R118, R132, R133: 0R05 1% 1W; R_1206_3216Metric_Pad1.24x1.80mm_HandSolder
R9, R80, R119: 2R2 1%; R_0402_1005Metric_Wbry
R10, R11, R12, R60, R61, R62, R63, R64, R120, R121, R122, R123: 47R 1%; R_0603_1608Metric_Wbry
R13, R98, R134: 60K4; R_0402_1005Metric_Wbry
R14, R16, R26, R42, R46, R49, R89, R90, R91, R99, R135: 4K7; R_0603_1608Metric_Wbry
R17, R108: 2K2; R_0402_1005Metric_Wbry
R18, R40, R43, R47: 180R; R_0402_1005Metric_Wbry
R20: 100K; R_0402_1005Metric_Wbry
R21, R36, R41, R45, R50, R52, R54, R56, R75: 1K; R_0402_1005Metric_Wbry
R25: 15R; R_0402_1005Metric_Wbry
R28, R34, R35: 2K2 0.1%; R_0603_1608Metric_Wbry
R31: 330R; R_0603_1608Metric_Wbry
R37, R38: 59R 1%; R_0402_1005Metric_Wbry
R65, R66, R67, R68, R69, R70, R71, R81, R107, R110, R111, R113, R114, R115, R116, R117, R124, R125, R126, R127, R128, R129, R130, R131: 150R; R_0402_1005Metric_Wbry
R76, R77: 1K - DNP; R_0402_1005Metric_Wbry
R95: 16K; R_0402_1005Metric_Wbry
R96: 5K1; R_0402_1005Metric_Wbry
R100, R101, R102, R103, R104, R112: 470R; R_0402_1005Metric_Wbry
R105, R106: 10R; R_0402_1005Metric_Wbry
R136: 4K7; R_0402_1005Metric_Wbry
S1: RESET; SW_SIDE_1_lugs
SW1: CAN ADDR; SW_DIP_SPSTx04_Slide_6.7x11.72mm_W7.62mm_P2.54mm_LowProfile
TP1: TP_D0; Test_Point_SMT_1x3
TP2: TP_D1; Test_Point_SMT_1x3
TP3: TP_D2; Test_Point_SMT_1x3
TP4: OUT_0; TestPoint_Pad_D2.0mm
TP5: OUT_1; TestPoint_Pad_D2.0mm
TP6: OUT_2; TestPoint_Pad_D2.0mm
TP7: OUT_3; TestPoint_Pad_D2.0mm
TP8: OUT_4; TestPoint_Pad_D2.0mm
TP9: OUT_5; TestPoint_Pad_D2.0mm
TP10: OUT_6; TestPoint_Pad_D2.0mm
TP11: OUT_7; TestPoint_Pad_D2.0mm
TP12: OUT_8; TestPoint_Pad_D2.0mm
TP13: DRIVER_CS; TestPoint_Pad_D2.0mm
TP14: DRIVER_ENN; TestPoint_Pad_D2.0mm
TP15: DRIVER_0_SDO; TestPoint_Pad_D2.0mm
TP16: DRIVER_1_SDO; TestPoint_Pad_D2.0mm
TP17: SPI0_MOSI; TestPoint_Pad_D2.0mm
TP18: SPI0_SCK; TestPoint_Pad_D2.0mm
TP19: SPI0_MISO; TestPoint_Pad_D2.0mm
TP20: D0_DIAG1; TestPoint_Pad_D2.0mm
TP21: D1_DIAG1; TestPoint_Pad_D2.0mm
TP22: D2_DIAG1; TestPoint_Pad_D2.0mm
TP23: 5V_INT; TestPoint_THTPad_D2.0mm_Drill1.0mm
TP24: +3.3V; TestPoint_THTPad_D2.0mm_Drill1.0mm
TR1, TR3, TR5: AOD4184A; TO-252-2_vias
U1, U2, U3: TMC5160; TMC5160-TA
U4: AP2127K-3.3; SOT-23-5
U5, U11: TS30041; QFN-16-1EP_3x3mm_P0.5mm_EP1.8x1.8mm
U6: SAME51N19; LQFP-100_14x14mm_P0.5mm
U7: MCP2542; SOIC-8_3.9x4.9mm_P1.27mm
U8, U9: 74HCT365; TSSOP-16_4.4x5mm_P0.65mm
U10: AP2127K-ADJ; SOT-23-5
X1: CRYSTAL_4PIN; Crystal_SMD_ECS-33B-4Pin_3.2x2.5mm

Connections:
3.3V_EXT: D10.1, J16.1, J17.1, J18.1, J19.1, J20.1, J21.1, R95.1
5V_EXT: D20.1, J16.5, J17.5, J18.5, J19.5, J20.5, J21.5
5V_INT: C68.1, C71.1, C74.1, C102.1, C103.1, D5.2, D21.1, R109.1, TP23.1, U4.1, U4.3, U7.3, U8.16, U9.16, U10.1, U10.3
12V_EXT: C123.1, D22.1, D24.2, J1.3, J29.3
12V_MON: C115.1, R134.2, R135.1, U6.10
12V_VG: C2.2, C17.2, C35.2, C122.1, D23.1, R134.1, U1.3, U1.4, U2.3, U2.4, U3.3, U3.4
+3.3V: C19.2, C37.2, C43.1, C52.1, C53.1, C54.1, C56.1, C57.1, C67.1, C81.2, C87.1, C91.1, D1.3, D2.3, D6.2, D8.3, J28.8, J32.3, L6.1, R2.2, R4.2, R8.2, R19.1, R23.2, R30.2, R36.1, R72.2, R74.2, R79.1, R83.2, R87.2, R88.2, TP24.1, U1.20, U1.21, U1.22, U2.20, U2.21, U2.22, U3.20, U3.21, U3.22, U4.5, U6.25, U6.30, U6.39, U6.51, U6.63, U6.77, U6.92, U7.5
/Headers/CAN_SHD_GND: C86.1, J22.7, J22.8, J23.7, J23.8, R20.1
/MOSFET outputs/out_0: R40.1, TR1.1
/MOSFET outputs/out_1: R43.1, TR3.1
/MOSFET outputs/out_2: R47.1, TR5.1
/MOSFET outputs/out_3: Q13.1, R41.1
/MOSFET outputs/out_4: Q14.4, R45.1
/MOSFET outputs/out_5: Q15.4, R50.1
/MOSFET outputs/out_6: Q13.4, R52.1
/MOSFET outputs/out_7: Q14.1, R54.1
/MOSFET outputs/out_8: Q15.1, R56.1
/Power/3.3_ADJ: R95.2, R96.1, U10.4
/Power/3.3_VOUT: C104.1, D10.2, U10.5
/Power/5V_BST: C46.2, U5.10
/Power/5V_COMMON: C49.1, D20.2, D21.2, L4.2
/Power/5V_FB: R108.1, R109.2, U5.5
/Power/5V_VCC: C42.1, C44.1, C45.1, L1.2, U5.2, U5.3, U5.11
/Power/5V_VSW: L3.2, R106.2, U5.1, U5.12, U5.13, U5.16
/Power/5_VOUT: C47.1, C48.1, L3.1, L4.1
/Power/12V_BST: C107.2, U11.10
/Power/12V_FB: R98.2, R99.1, U11.5
/Power/12V_VCC: C73.1, C105.1, C106.1, L2.2, U11.2, U11.3, U11.11
/Power/12V_VSW: L8.2, R105.2, U11.1, U11.12, U11.13, U11.16
/Power/12_VOUT: C108.1, C109.1, L8.1, L9.1, R98.1
/Power/L9_OUT: C110.1, D22.2, D23.2, L9.2
/Processor/CANH_C: L7.2, U7.7
/Processor/CANL_C: L7.1, U7.6
/Processor/IO_0_OUT_R: R112.2, U6.52
/Processor/IO_1_OUT_R: R104.2, U6.64
/Processor/IO_2_OUT_R: R103.2, U6.68
/Processor/IO_3_OUT_R: R100.1, U6.17
/Processor/IO_4_OUT_R: R101.2, U6.96
/Processor/IO_5_OUT_R: R102.2, U6.70
/Processor/RESET_SW: R31.1, S1.3, S1.4
/Processor/VDDCORE: C60.1, C61.1, U6.89
/Processor/XIN0: C66.1, U6.48, X1.3
/Processor/XOUT0: C62.1, U6.49, X1.1
/Processor/_RESET: C64.1, D9.1, R31.2
/Processor/out_3_tach: R84.1, U6.46
/Processor/out_4_tach: R86.2, U6.67
/Processor/out_5_tach: R85.2, U6.61
/Stepper Driver & Endstops/D0_5VOUT: C98.2, R80.1, U1.5
/Stepper Driver & Endstops/D0_CA1: C4.2, U1.42
/Stepper Driver & Endstops/D0_CA2: C8.2, U1.35
/Stepper Driver & Endstops/D0_CB1: C5.2, U1.2
/Stepper Driver & Endstops/D0_CB2: C9.2, U1.43
/Stepper Driver & Endstops/D0_CPI: C10.2, U1.31
/Stepper Driver & Endstops/D0_CPO: C10.1, U1.32
/Stepper Driver & Endstops/D0_HA1: D26.4, R107.1, U1.41
/Stepper Driver & Endstops/D0_HA2: D25.6, R111.1, U1.36
/Stepper Driver & Endstops/D0_HAG1: D26.3, Q1.4, R107.2
/Stepper Driver & Endstops/D0_HAG2: D25.1, Q2.1, R111.2
/Stepper Driver & Endstops/D0_HB1: D28.4, R115.1, U1.1
/Stepper Driver & Endstops/D0_HB2: D27.6, R114.1, U1.44
/Stepper Driver & Endstops/D0_HBG1: D28.3, Q3.4, R115.2
/Stepper Driver & Endstops/D0_HBG2: D27.1, Q4.1, R114.2
/Stepper Driver & Endstops/D0_LA1: D26.6, R110.1, U1.39
/Stepper Driver & Endstops/D0_LA2: D25.4, R113.1, U1.38
/Stepper Driver & Endstops/D0_LAG1: D26.1, Q1.1, R110.2
/Stepper Driver & Endstops/D0_LAG2: D25.3, Q2.4, R113.2
/Stepper Driver & Endstops/D0_LB1: D28.6, R116.1, U1.47
/Stepper Driver & Endstops/D0_LB2: D27.4, R117.1, U1.46
/Stepper Driver & Endstops/D0_LBG1: D28.1, Q3.1, R116.2
/Stepper Driver & Endstops/D0_LBG2: D27.3, Q4.4, R117.2
/Stepper Driver & Endstops/D0_SRAH: C16.2, R60.1, U1.8
/Stepper Driver & Endstops/D0_SRAL: C16.1, R61.1, U1.7
/Stepper Driver & Endstops/D0_SRAT: Q1.2, Q2.3, R5.2, R60.2
/Stepper Driver & Endstops/D0_SRBH: C6.2, R62.1, U1.9
/Stepper Driver & Endstops/D0_SRBL: C6.1, R63.1, U1.10
/Stepper Driver & Endstops/D0_SRBT: Q3.2, Q4.3, R6.2, R62.2
/Stepper Driver & Endstops/D0_VCC: C92.2, R80.2, U1.29
/Stepper Driver & Endstops/D0_VCP: C7.1, U1.34
/Stepper Driver & Endstops/D1_5VOUT: C18.2, R9.1, U2.5
/Stepper Driver & Endstops/D1_CA1: C26.2, U2.42
/Stepper Driver & Endstops/D1_CA2: C22.2, U2.35
/Stepper Driver & Endstops/D1_CB1: C25.2, U2.2
/Stepper Driver & Endstops/D1_CB2: C21.2, U2.43
/Stepper Driver & Endstops/D1_CPI: C24.2, U2.31
/Stepper Driver & Endstops/D1_CPO: C24.1, U2.32
/Stepper Driver & Endstops/D1_HA1: D30.4, R70.1, U2.41
/Stepper Driver & Endstops/D1_HA2: D29.6, R69.1, U2.36
/Stepper Driver & Endstops/D1_HAG1: D30.3, Q5.4, R70.2
/Stepper Driver & Endstops/D1_HAG2: D29.1, Q7.1, R69.2
/Stepper Driver & Endstops/D1_HB1: D32.4, R66.1, U2.1
/Stepper Driver & Endstops/D1_HB2: D31.6, R65.1, U2.44
/Stepper Driver & Endstops/D1_HBG1: D32.3, Q6.4, R66.2
/Stepper Driver & Endstops/D1_HBG2: D31.1, Q8.1, R65.2
/Stepper Driver & Endstops/D1_LA1: D30.6, R71.1, U2.39
/Stepper Driver & Endstops/D1_LA2: D29.4, R81.1, U2.38
/Stepper Driver & Endstops/D1_LAG1: D30.1, Q5.1, R71.2
/Stepper Driver & Endstops/D1_LAG2: D29.3, Q7.4, R81.2
/Stepper Driver & Endstops/D1_LB1: D32.6, R67.1, U2.47
/Stepper Driver & Endstops/D1_LB2: D31.4, R68.1, U2.46
/Stepper Driver & Endstops/D1_LBG1: D32.1, Q6.1, R67.2
/Stepper Driver & Endstops/D1_LBG2: D31.3, Q8.4, R68.2
/Stepper Driver & Endstops/D1_SRAH: C34.2, R12.1, U2.8
/Stepper Driver & Endstops/D1_SRAL: C34.1, R64.1, U2.7
/Stepper Driver & Endstops/D1_SRAT: Q5.2, Q7.3, R12.2, R82.2
/Stepper Driver & Endstops/D1_SRBH: C111.2, R10.1, U2.9
/Stepper Driver & Endstops/D1_SRBL: C111.1, R11.1, U2.10
/Stepper Driver & Endstops/D1_SRBT: Q6.2, Q8.3, R10.2, R118.2
/Stepper Driver & Endstops/D1_VCC: C20.2, R9.2, U2.29
/Stepper Driver & Endstops/D1_VCP: C23.1, U2.34
/Stepper Driver & Endstops/D2_5VOUT: C36.2, R119.1, U3.5
/Stepper Driver & Endstops/D2_CA1: C82.2, U3.42
/Stepper Driver & Endstops/D2_CA2: C77.2, U3.35
/Stepper Driver & Endstops/D2_CB1: C80.2, U3.2
/Stepper Driver & Endstops/D2_CB2: C39.2, U3.43
/Stepper Driver & Endstops/D2_CPI: C79.2, U3.31
/Stepper Driver & Endstops/D2_CPO: C79.1, U3.32
/Stepper Driver & Endstops/D2_HA1: D34.4, R129.1, U3.41
/Stepper Driver & Endstops/D2_HA2: D33.6, R128.1, U3.36
/Stepper Driver & Endstops/D2_HAG1: D34.3, Q9.4, R129.2
/Stepper Driver & Endstops/D2_HAG2: D33.1, Q11.1, R128.2
/Stepper Driver & Endstops/D2_HB1: D36.4, R125.1, U3.1
/Stepper Driver & Endstops/D2_HB2: D35.6, R124.1, U3.44
/Stepper Driver & Endstops/D2_HBG1: D36.3, Q10.4, R125.2
/Stepper Driver & Endstops/D2_HBG2: D35.1, Q12.1, R124.2
/Stepper Driver & Endstops/D2_LA1: D34.6, R130.1, U3.39
/Stepper Driver & Endstops/D2_LA2: D33.4, R131.1, U3.38
/Stepper Driver & Endstops/D2_LAG1: D34.1, Q9.1, R130.2
/Stepper Driver & Endstops/D2_LAG2: D33.3, Q11.4, R131.2
/Stepper Driver & Endstops/D2_LB1: D36.6, R126.1, U3.47
/Stepper Driver & Endstops/D2_LB2: D35.4, R127.1, U3.46
/Stepper Driver & Endstops/D2_LBG1: D36.1, Q10.1, R126.2
/Stepper Driver & Endstops/D2_LBG2: D35.3, Q12.4, R127.2
/Stepper Driver & Endstops/D2_SRAH: C113.2, R122.1, U3.8
/Stepper Driver & Endstops/D2_SRAL: C113.1, R123.1, U3.7
/Stepper Driver & Endstops/D2_SRAT: Q9.2, Q11.3, R122.2, R132.2
/Stepper Driver & Endstops/D2_SRBH: C112.2, R120.1, U3.9
/Stepper Driver & Endstops/D2_SRBL: C112.1, R121.1, U3.10
/Stepper Driver & Endstops/D2_SRBT: Q10.2, Q12.3, R120.2, R133.2
/Stepper Driver & Endstops/D2_VCC: C38.2, R119.2, U3.29
/Stepper Driver & Endstops/D2_VCP: C78.1, U3.34
BOARD_ID_0: SW1.8, U6.41
BOARD_ID_1: SW1.7, U6.42
BOARD_ID_2: SW1.6, U6.44
BOARD_ID_3: SW1.5, U6.45
BOARD_TYPE_0: R75.1, U6.66
BOARD_TYPE_1: R76.1, U6.58
BOARD_TYPE_2: R77.1, U6.43
CAN1RX: U6.35, U7.4
CAN1TX: U6.34, U7.1
CAN_H: J22.3, J23.3, JP2.1, L7.3
CAN_L: J22.4, J23.4, JP2.4, L7.4
DIAG_LED: R21.1, U6.40
DRIVER_0_A1: C4.1, C11.2, J24.2, Q1.3, Q1.5, U1.40
DRIVER_0_A2: C8.1, C12.2, J24.1, Q2.2, Q2.6, U1.37
DRIVER_0_B1: C5.1, C13.2, J24.4, Q3.3, Q3.5, U1.48
DRIVER_0_B2: C9.1, C14.2, J24.3, Q4.2, Q4.6, U1.45
DRIVER_0_DIAG0: TP1.3, U1.26, U6.27
DRIVER_0_DIAG1: TP20.1, U1.27, U6.72
DRIVER_0_DIR: TP1.2, U1.18, U6.73
DRIVER_0_SDO: TP15.1, U1.16, U2.15
DRIVER_0_STEP: R91.1, TP1.1, U1.17, U6.75
DRIVER_1_A1: C26.1, C30.2, J25.2, Q5.3, Q5.5, U2.40
DRIVER_1_A2: C22.1, C31.2, J25.1, Q7.2, Q7.6, U2.37
DRIVER_1_B1: C25.1, C32.2, J25.4, Q6.3, Q6.5, U2.48
DRIVER_1_B2: C21.1, C33.2, J25.3, Q8.2, Q8.6, U2.45
DRIVER_1_DIAG0: TP2.3, U2.26, U6.85
DRIVER_1_DIAG1: TP21.1, U2.27, U6.84
DRIVER_1_DIR: TP2.2, U2.18, U6.86
DRIVER_1_SDO: TP16.1, U2.16, U3.15
DRIVER_1_STEP: R90.1, TP2.1, U2.17, U6.87
DRIVER_2_A1: C82.1, C96.2, J26.2, Q9.3, Q9.5, U3.40
DRIVER_2_A2: C77.1, C97.2, J26.1, Q11.2, Q11.6, U3.37
DRIVER_2_B1: C80.1, C99.2, J26.4, Q10.3, Q10.5, U3.48
DRIVER_2_B2: C39.1, C100.2, J26.3, Q12.2, Q12.6, U3.45
DRIVER_2_DIAG0: TP3.3, U3.26, U6.95
DRIVER_2_DIAG1: TP22.1, U3.27, U6.97
DRIVER_2_DIR: TP3.2, U3.18, U6.1
DRIVER_2_STEP: R89.1, TP3.1, U3.17, U6.2
DRIVER_CS: R79.2, TP13.1, U1.13, U2.13, U3.13, U6.78
DRIVER_ENN: R19.2, TP14.1, U1.28, U2.28, U3.28, U6.79
GND: C1.2, C2.1, C3.2, C11.1, C12.1, C13.1, C14.1, C15.2, C17.1, C18.1, C19.1, C20.1, C27.2, C28.1, C29.1, C30.1, C31.1, C32.1, C33.1, C35.1, C36.1, C37.1, C38.1, C40.2, C41.2, C42.2, C43.2, C44.2, C45.2, C47.2, C48.2, C49.2, C50.2, C51.2, C52.2, C53.2, C54.2, C56.2, C57.2, C58.2, C59.2, C60.2, C61.2, C62.2, C64.2, C66.2, C67.2, C68.2, C69.1, C70.2, C71.2, C72.2, C73.2, C74.2, C75.1, C76.1, C81.1, C83.2, C84.2, C85.2, C86.2, C87.2, C88.2, C89.2, C90.2, C91.2, C92.1, C93.2, C94.1, C95.1, C96.1, C97.1, C98.1, C99.1, C100.1, C101.2, C102.2, C103.2, C104.2, C105.2, C106.2, C108.2, C109.2, C110.2, C114.1, C115.2, C116.1, C117.1, C118.1, C119.1, C120.1, C121.2, C122.2, C123.2, D7.1, J2.2, J6.1, J7.1, J8.1, J9.1, J16.3, J17.3, J18.3, J19.3, J20.3, J21.3, J28.2, J32.6, NT1.2, NT2.2, Q13.2, Q13.3, Q14.2, Q14.3, Q15.2, Q15.3, R5.1, R6.1, R11.2, R14.2, R16.2, R17.2, R18.2, R20.2, R39.1, R44.1, R48.1, R51.1, R53.1, R55.1, R57.1, R58.1, R59.1, R61.2, R63.2, R64.2, R75.2, R76.2, R77.2, R78.2, R82.1, R89.2, R90.2, R91.2, R96.2, R99.2, R108.2, R118.1, R121.2, R123.2, R132.1, R133.1, R135.2, R136.2, S1.1, S1.2, SW1.1, SW1.2, SW1.3, SW1.4, TR1.3, TR3.3, TR5.3, U1.6, U1.11, U1.12, U1.19, U1.23, U1.24, U1.30, U1.EPAD, U2.6, U2.11, U2.12, U2.19, U2.23, U2.24, U2.30, U2.EPAD, U3.6, U3.11, U3.12, U3.19, U3.23, U3.24, U3.30, U3.EPAD, U4.2, U5.4, U5.14, U5.15, U5.17, U6.24, U6.31, U6.38, U6.50, U6.62, U6.76, U6.90, U7.2, U7.8, U8.1, U8.8, U8.10, U8.12, U8.14, U8.15, U9.1, U9.8, U9.15, U10.2, U11.4, U11.14, U11.15, U11.17, X1.2, X1.4
GNDANA: C55.2, C63.2, C65.2, F2.2, NT1.1, NT2.1, U6.11
IO_0: C88.1, D1.1, R22.1, U6.19
IO_0_IN: J19.2, R22.2, R23.1, R92.2
IO_0_OUT: J19.4, R112.1
IO_1: C89.1, D8.1, R24.1, U6.5
IO_1_IN: J20.2, R24.2, R72.1, R93.2
IO_1_OUT: J20.4, R104.1
IO_2: C90.1, D2.2, R73.1, U6.3
IO_2_IN: J21.2, R73.2, R74.1, R94.2
IO_2_OUT: J21.4, R103.1
IO_3: C1.1, D1.2, R1.1, U6.60
IO_3_IN: J16.2, R1.2, R2.1
IO_3_OUT: J16.4, R100.2
IO_4: C3.1, D8.2, R3.1, U6.82
IO_4_IN: J17.2, R3.2, R4.1
IO_4_OUT: J17.4, R101.1
IO_5: C15.1, D2.1, R7.1, U6.4
IO_5_IN: J18.2, R7.2, R8.1
IO_5_OUT: J18.4, R102.1
unnamed: C46.1, R106.1
unnamed: C69.2, R37.2, R38.1
unnamed: C107.1, R105.1
unnamed: D4.1, R16.1
unnamed: D5.1, R17.1
unnamed: D6.1, R18.1
unnamed: D7.2, R21.2
unnamed: D11.2, R42.1
unnamed: D13.2, R46.1
unnamed: D15.2, R49.1
unnamed: D24.1, R136.1
unnamed: JP2.2, R37.1
unnamed: JP2.3, R38.2
OUT_0: R57.2, TP4.1, U6.54, U8.2
OUT_0_BUFF: R40.2, U8.3
OUT_0_NEG: D11.1, J10.1, TR1.2
OUT_1: R58.2, TP5.1, U6.55, U8.4
OUT_1_BUFF: R43.2, U8.5
OUT_1_NEG: D13.1, J11.1, TR3.2
OUT_2: R59.2, TP6.1, U6.74, U8.6
OUT_2_BUFF: R47.2, U8.7
OUT_2_NEG: D15.1, J12.1, TR5.2
OUT_3: R51.2, TP7.1, U6.16, U9.10
OUT_3_BUFF: R41.2, U9.9
OUT_3_NEG: D12.2, J6.4, Q13.5
OUT_3_TACHO: J6.3, R83.1, R84.2
OUT_4: R53.2, TP8.1, U6.18, U9.12
OUT_4_BUFF: R45.2, U9.11
OUT_4_NEG: D14.2, J7.4, Q14.6
OUT_4_TACHO: J7.3, R86.1, R87.1
OUT_5: R55.2, TP9.1, U6.26, U9.14
OUT_5_BUFF: R50.2, U9.13
OUT_5_NEG: D16.2, J8.4, Q15.6
OUT_5_TACHO: J8.3, R85.1, R88.1
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

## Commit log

2020-02-28 Added Schematic and Step file
2020-06-17 Added wiring & dimension svgs
2020-09-11 Fixed typos in wiring diagram
2020-11-23 Added KiCAD project
    [Comms.sch, Duet3_Exp_3HC.kicad_pcb, Duet3_Exp_3HC.sch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]
